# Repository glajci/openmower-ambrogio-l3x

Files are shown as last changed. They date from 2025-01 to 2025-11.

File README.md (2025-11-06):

# Openmower - Ambrogio - L3x
Convert Ambrogio L30 mower to [OpenMower](https://openmower.de) powered mower.

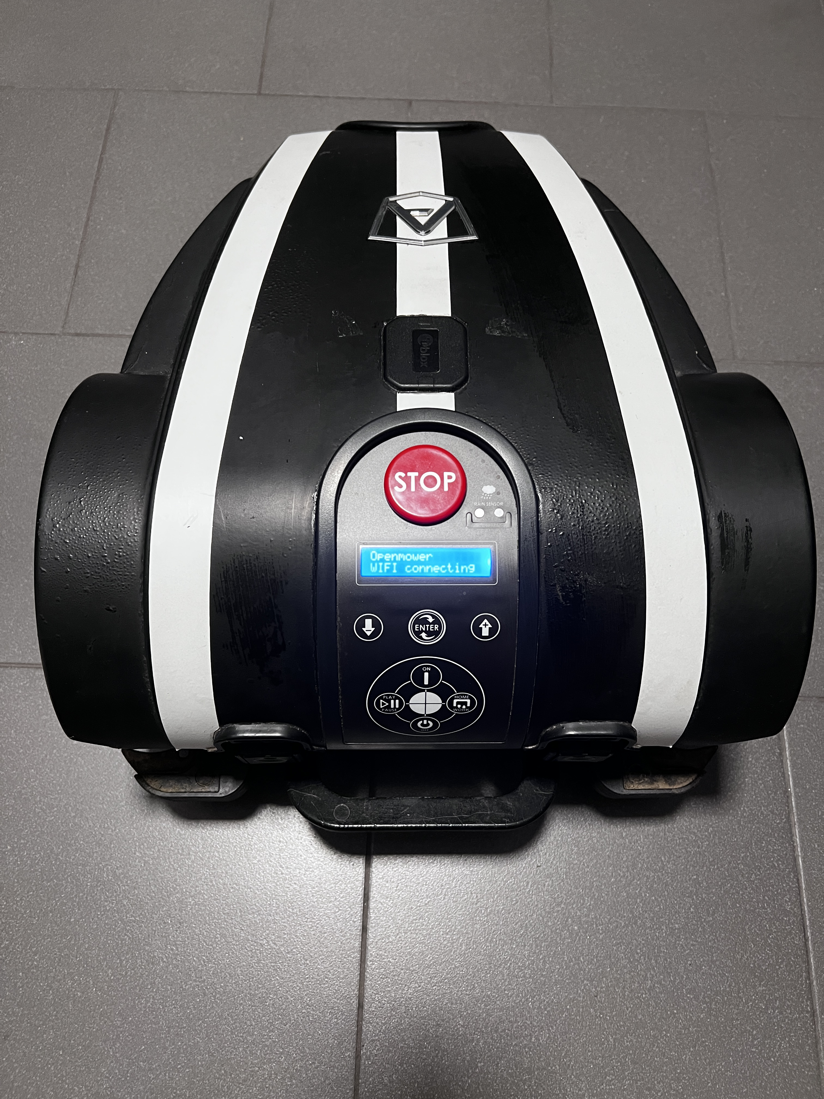
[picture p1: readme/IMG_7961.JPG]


> [!WARNING]
> Please be aware that this is a working prototype, any modifications to the mower are made at your own risk.

> [!NOTE]
> Ambrogio L30 mower was used in this project, but it should work with Viper C6, Stiga Autoclip 225 and similar as well.

# Features

* All of the features of the [OpenMower](https://openmower.de)
* Rain sensor
* Lift Sensor
* Emergency Stop push button
* Cutting with 25cm
* Integrated built-in display and top cover buttons (optional)

> Comparison with Yard Force Classic 500
> * Pros:
>   * Increased cutting width (25cm)
>   * More powerful, no issues with cutting the grass
>   * Turns easier due to its geometry
>   * No issues with steep climbs (no wheel spikes needed)
>
> * Cons:
>   * Louder mowing motor (while using 4 points steel cutting blade, perhaps 12 points plastic disc is quieter?)
>   * Tilt sensor not connected

# Hardware and Tools

You will need:

* Ambrogio L30 mower or similar (Viper C6, Stiga Autoclip 225 ...)
* [Open Mower Hardware Kit](https://shop.devops.care/10-openmower)
* [Ardusimple simpleRTK2B – Basic Starter Kit](https://www.ardusimple.com/product/simplertk2b-basic-starter-kit-ip65/)
* Raspberry Pi 4 (minimum 2GB)
* SD Card 16GB+
* USB Wi-Fi Dongle
* Yard Force Classic 500 wiring harnesses (can be created from the scratch as well)
* 3D printer
* [Vesc Tool Free](https://vesc-project.com/node/17)
* 16x2 LCD Display with I2C adapter (optional)
* 2 relay module (optional)

# Assembly

## Docking station

Remove all the original electronics from the docking station.

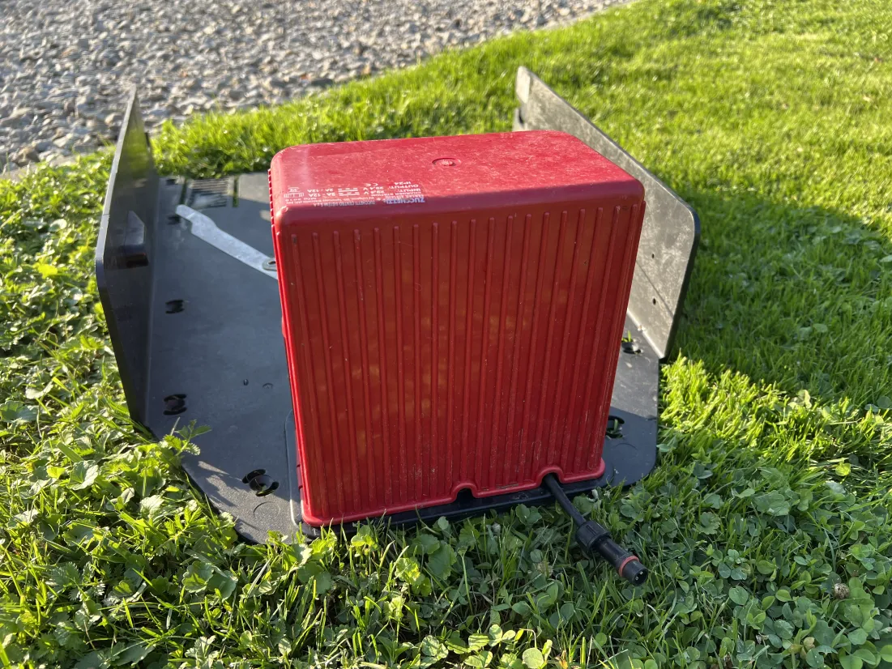
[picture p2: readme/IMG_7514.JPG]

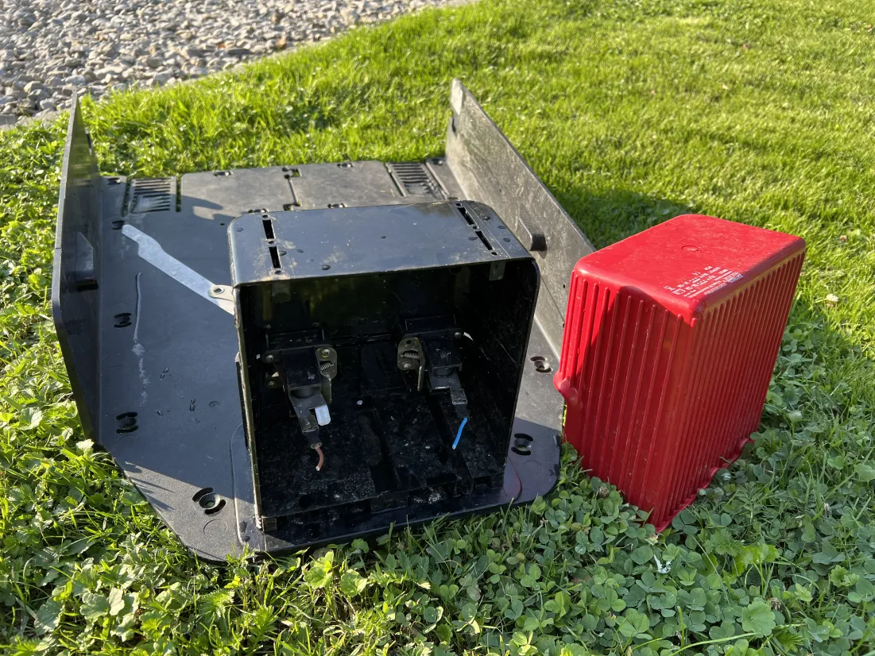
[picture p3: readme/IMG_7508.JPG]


Place 2 expansions plugs in 2 holes.

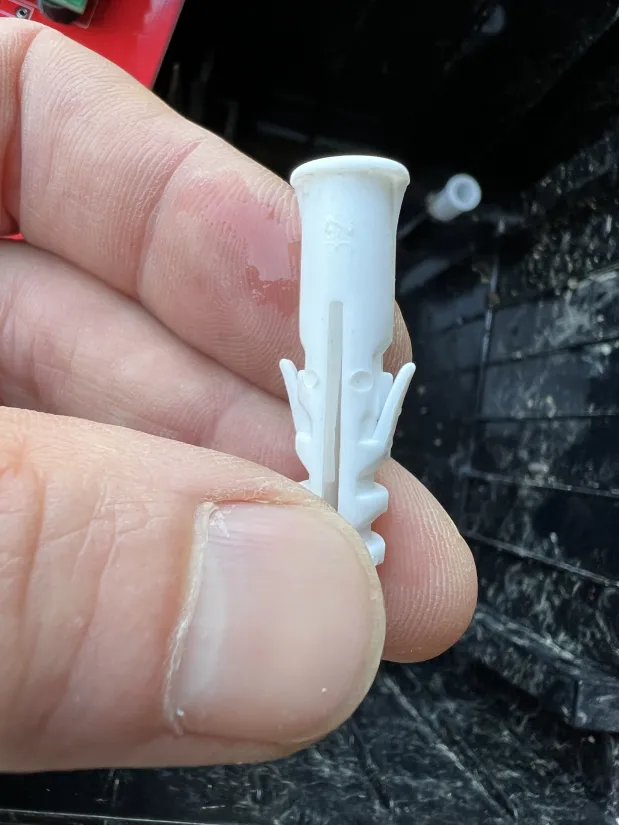
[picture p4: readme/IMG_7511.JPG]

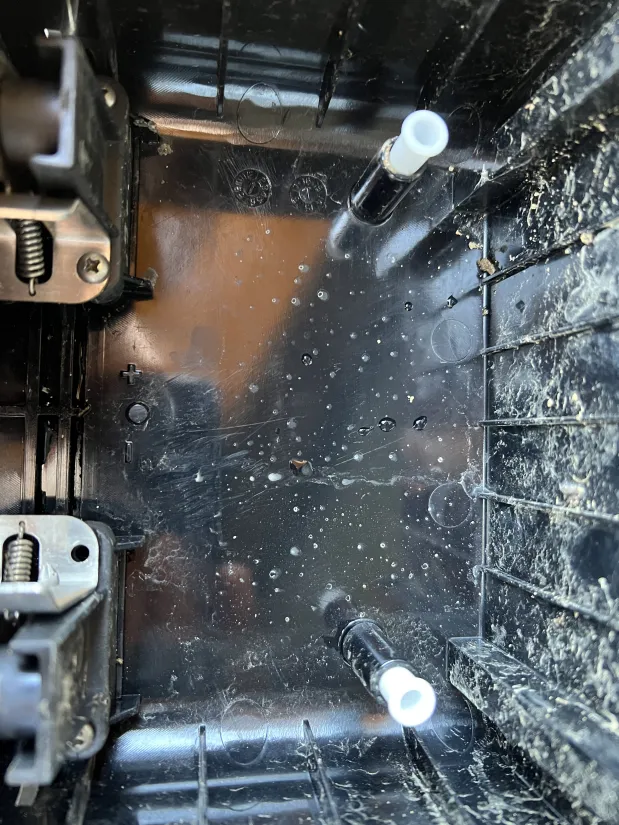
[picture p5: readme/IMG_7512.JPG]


Screw the DC/DC board

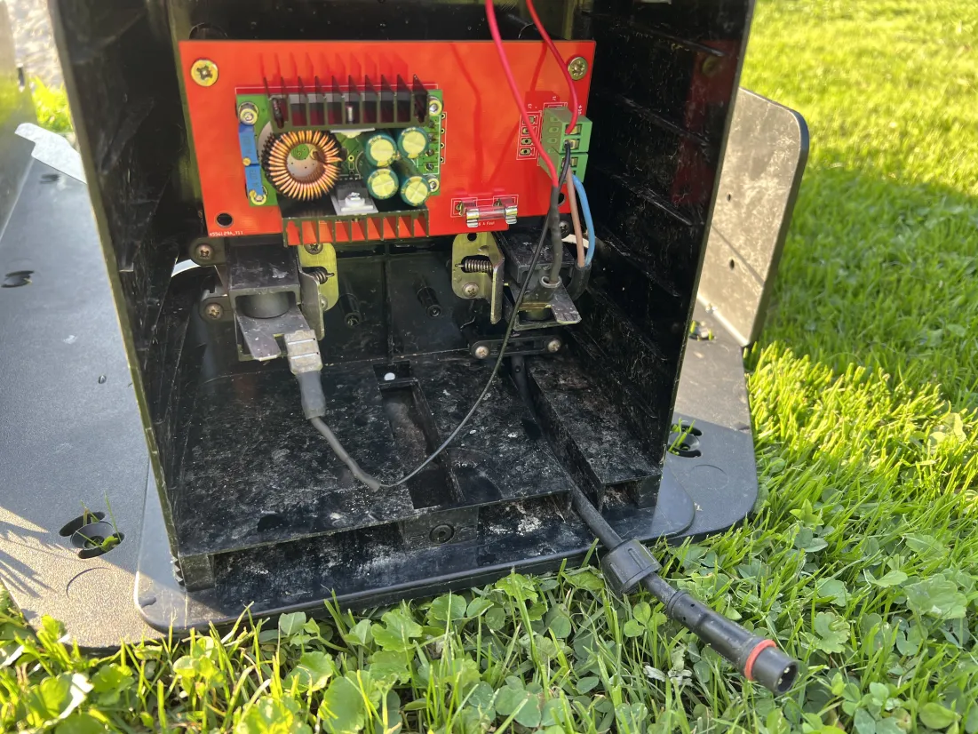
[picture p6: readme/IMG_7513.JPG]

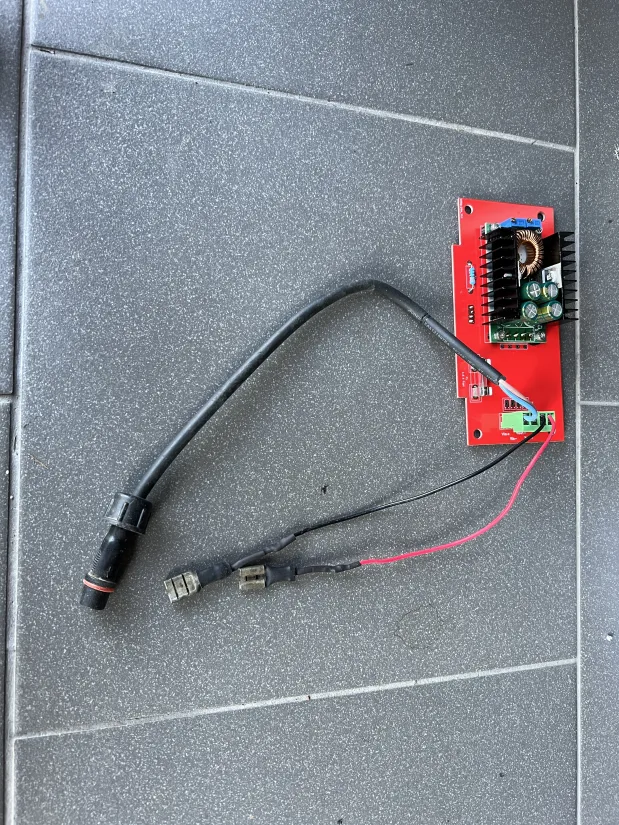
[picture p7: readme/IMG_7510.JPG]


> [!NOTE]
> Plug from the YardForce Classic 500 power supply was used here but the original Ambrogio power supply will work as well.
(find the positive and negative wires and connect it appropriately to the DC/DC board)

> [!NOTE]
> For all the voltage and current adjustments please follow the official [OpenMower](https://openmower.de) documentation.

## The mower

Remove all the original mower electronics.
Cut the plastic elements (see the pictures below) to make the place for the mainboard.

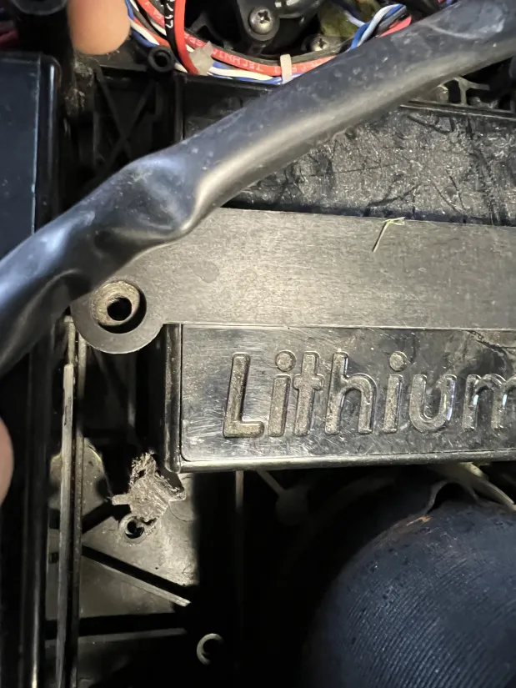
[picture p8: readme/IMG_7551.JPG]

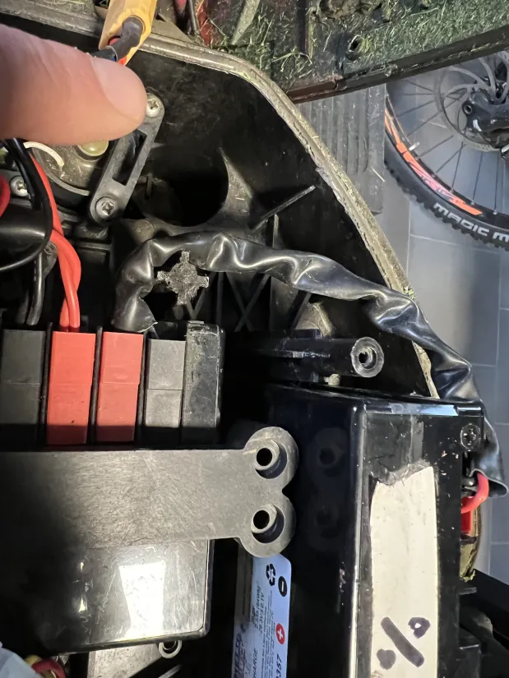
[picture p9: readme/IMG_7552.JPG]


### Prepare the motor Hall sensor wires.

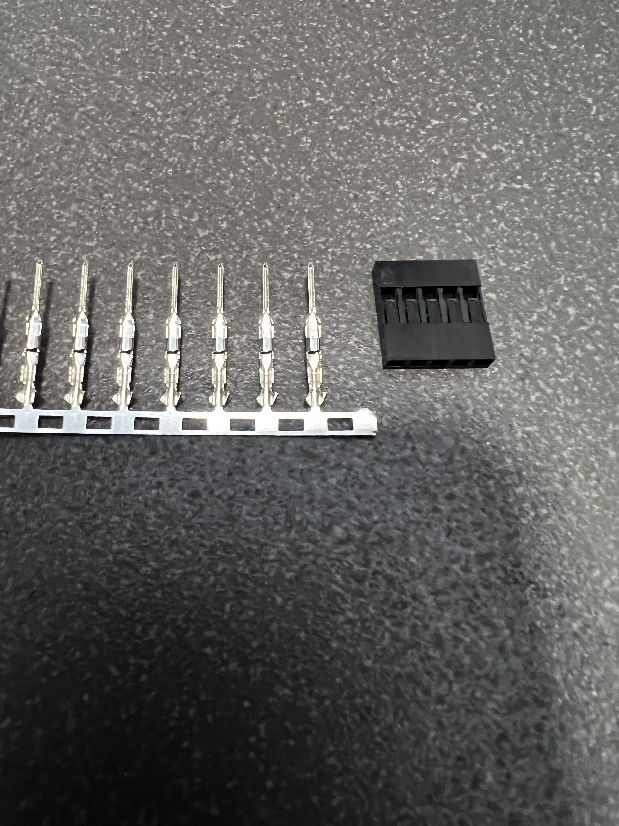
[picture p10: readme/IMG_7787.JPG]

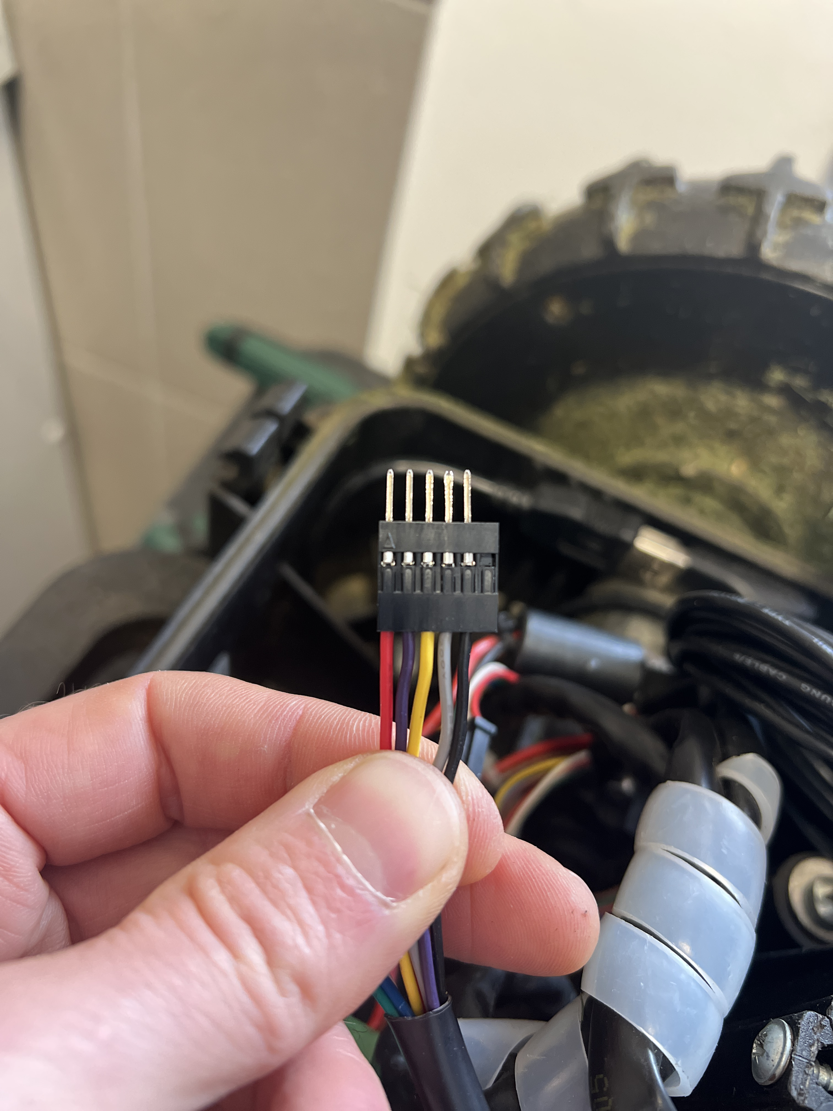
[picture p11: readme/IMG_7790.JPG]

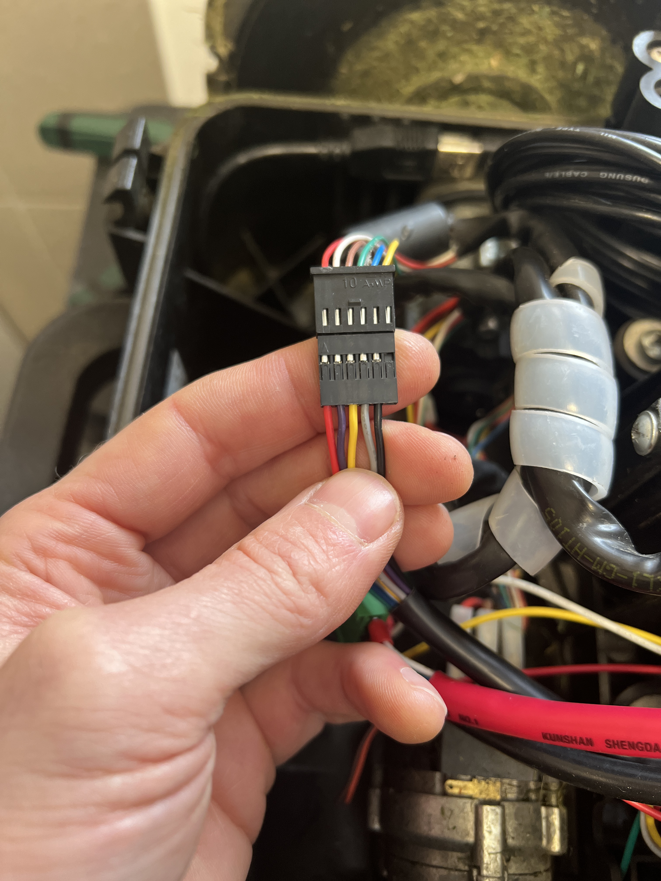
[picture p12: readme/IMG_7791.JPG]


### Prepare the motor power wires.

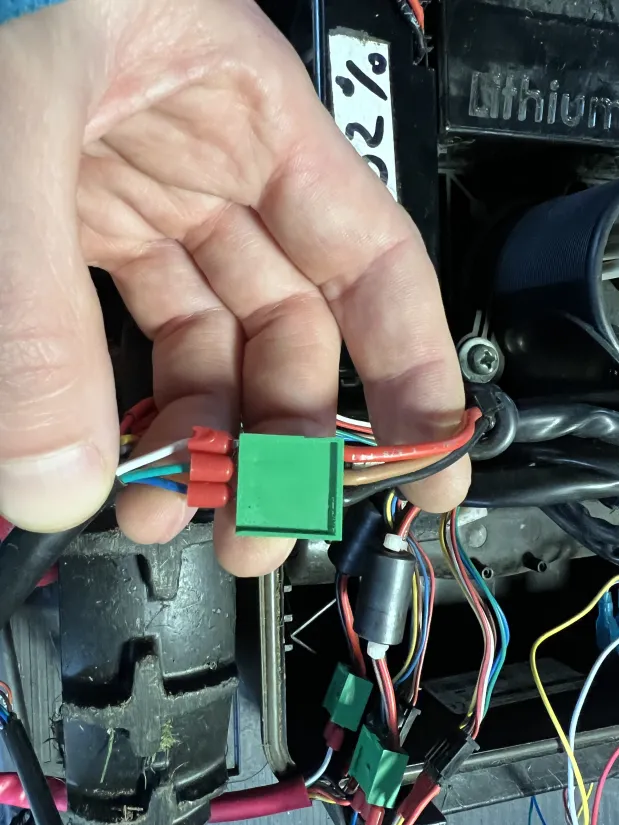
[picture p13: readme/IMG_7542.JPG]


### Ambrogio L30 Opemnower wiring diagram.

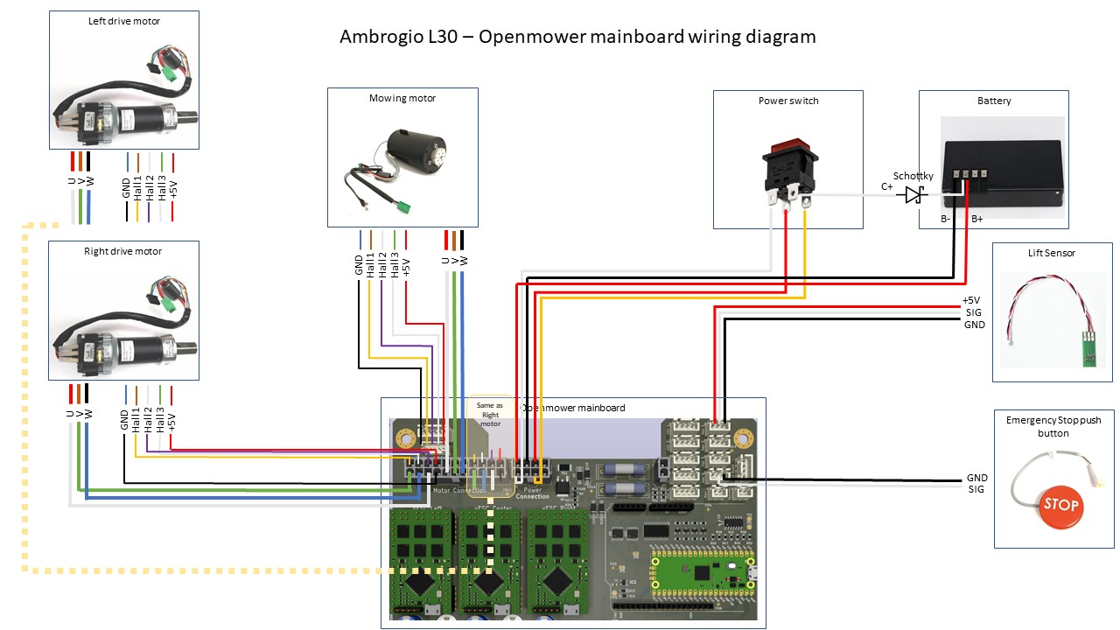
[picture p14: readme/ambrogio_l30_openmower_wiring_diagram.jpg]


> [!NOTE]
> YardForce Classic 500 wiring harness was used, since it fits to the OpenMower mainboard sockets, but it can be created from the scratch as well.

> [!NOTE]
> Crimped terminals for the motor power wires were used.

> [!NOTE]
> All 3 motor harnesses have the same colouring.

### Install the main switch into the mower body (power switch from the YardeForce Classic 500 was used here)
> [!NOTE]
> No need to install the power button if 2 relay module and top cover power buttons are integrated (see later in this tutorial).

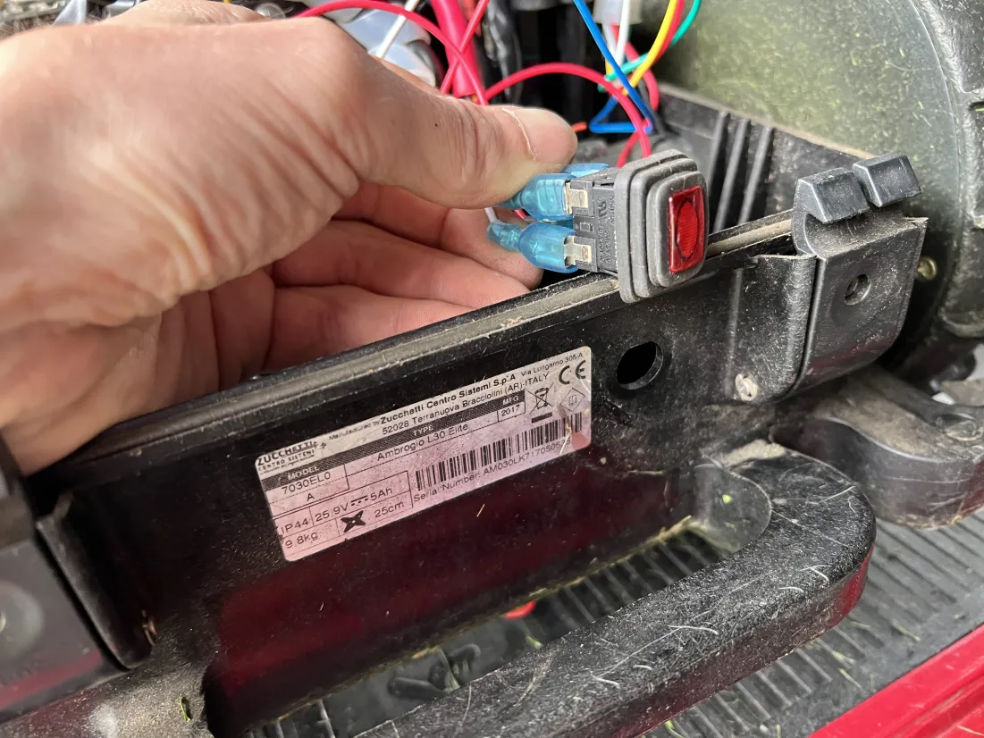
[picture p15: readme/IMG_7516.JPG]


Remove Ambrogio's power supply socket

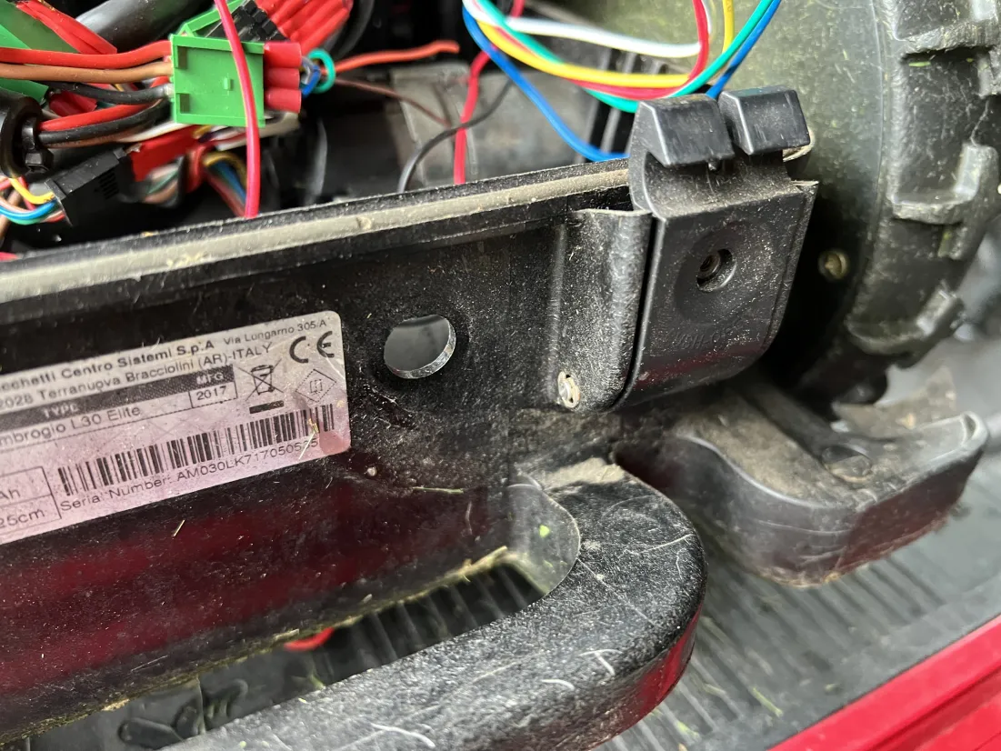
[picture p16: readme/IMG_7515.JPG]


Extend the circular hole to give it a rectangular shape with proper dimensions

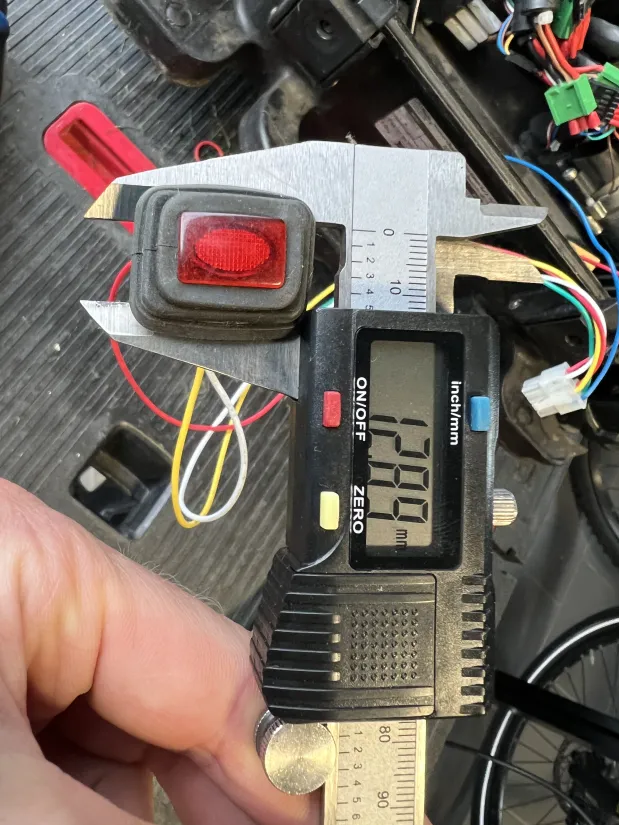
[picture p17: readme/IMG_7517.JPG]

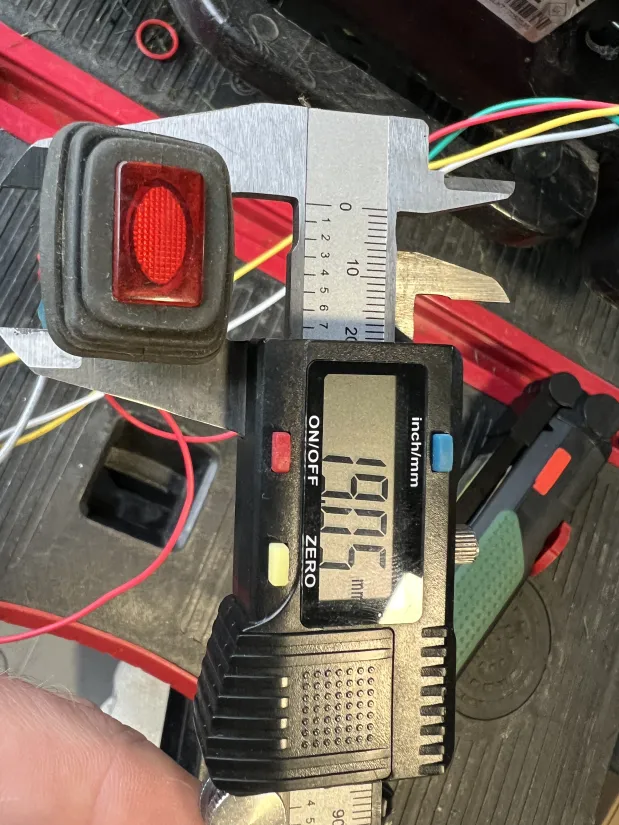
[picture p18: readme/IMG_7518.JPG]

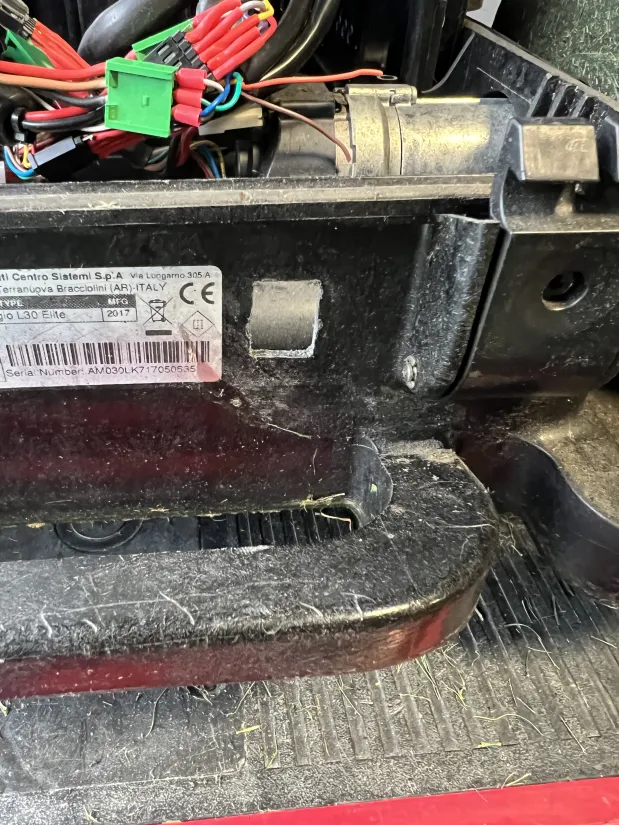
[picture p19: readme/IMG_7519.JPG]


Insert the power switch

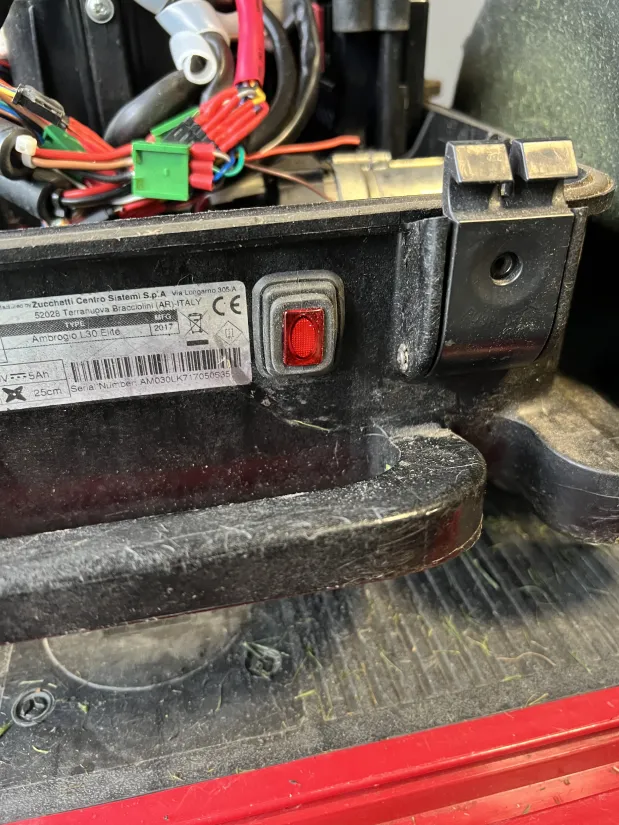
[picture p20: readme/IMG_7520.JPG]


### Prepare the power supply harness.
> [!NOTE]
> Since the Ambrogio batteries have just 2 wires (positive and negative), Shottky diode was used to create separate charge + and battery + signals. (Original YardForce Classic 500 battery plug was use here)

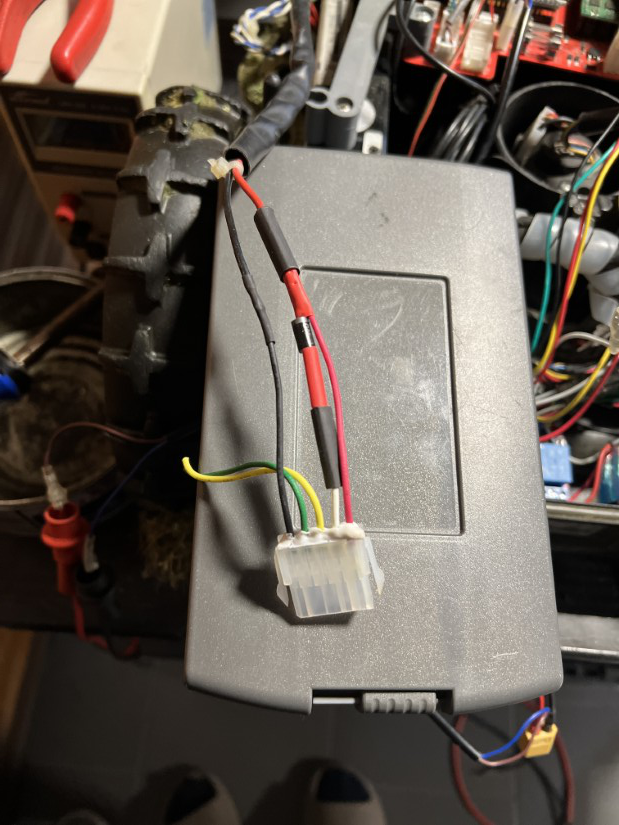
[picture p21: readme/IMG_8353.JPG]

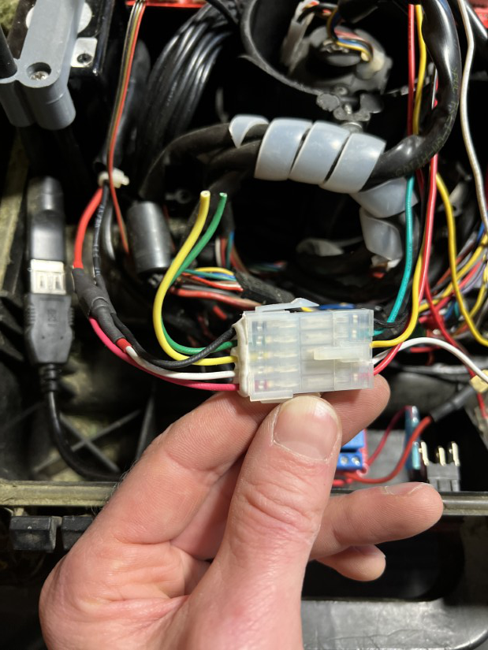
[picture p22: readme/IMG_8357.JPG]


Prepare the power connectors

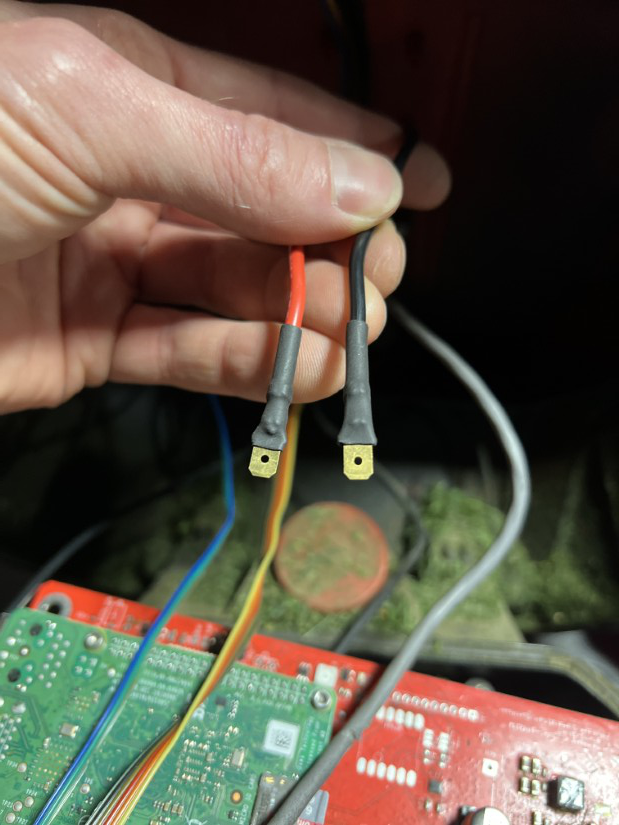
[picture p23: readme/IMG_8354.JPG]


Connect it to the OpenMower mainboard.

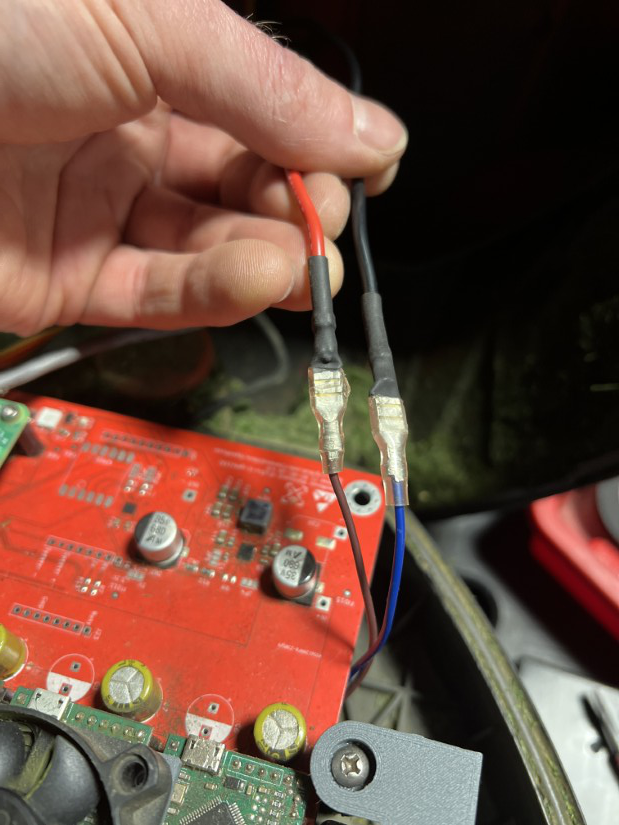
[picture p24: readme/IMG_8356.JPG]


Connect OpenMower with power button (2 relay module visible on the pictures is optional - see later in this tutorial).

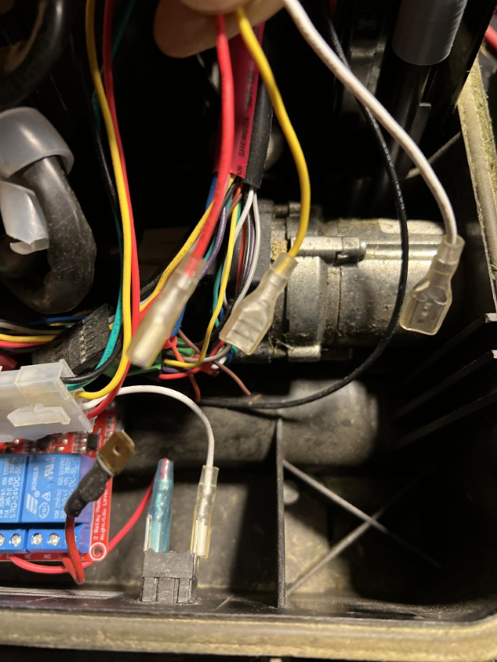
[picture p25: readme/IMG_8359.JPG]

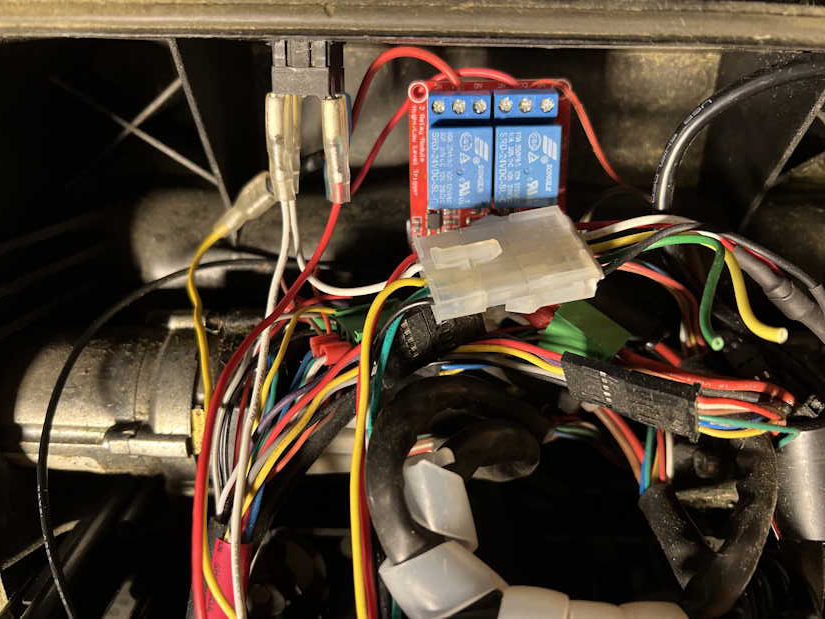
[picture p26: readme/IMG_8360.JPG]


### Prepare the lift sensor cable.

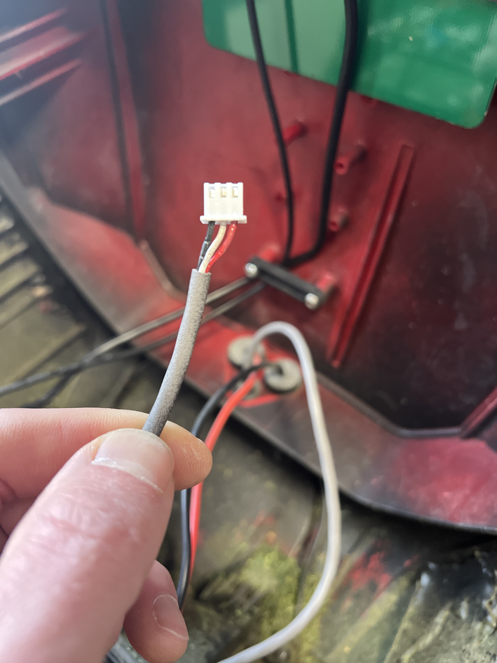
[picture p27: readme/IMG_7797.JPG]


### Install the mainboard

Unscrew the original left and right battery holders.
Print and screw the mainboard holders.
> [!NOTE]
> You will find all the 3d models in this repository.

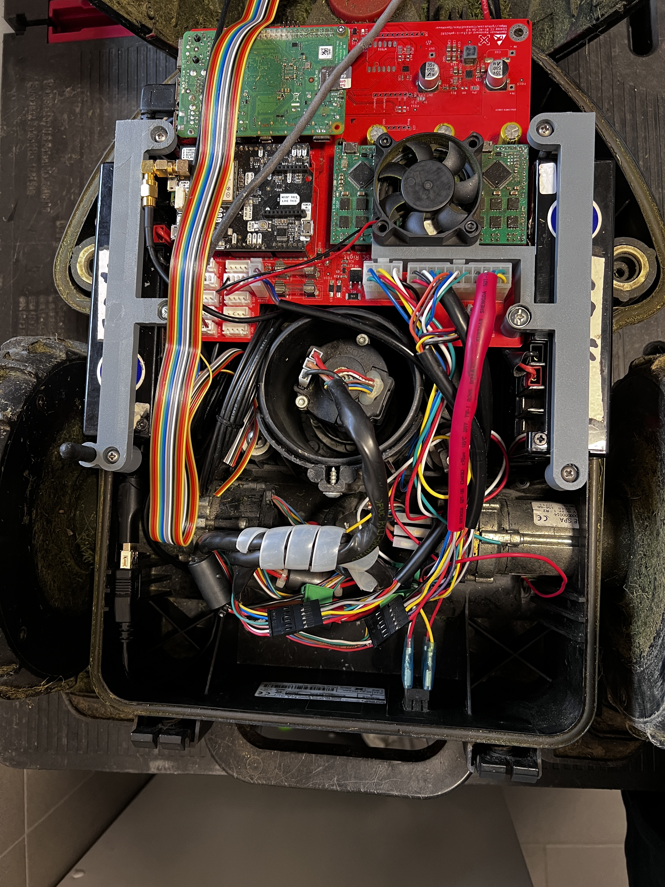
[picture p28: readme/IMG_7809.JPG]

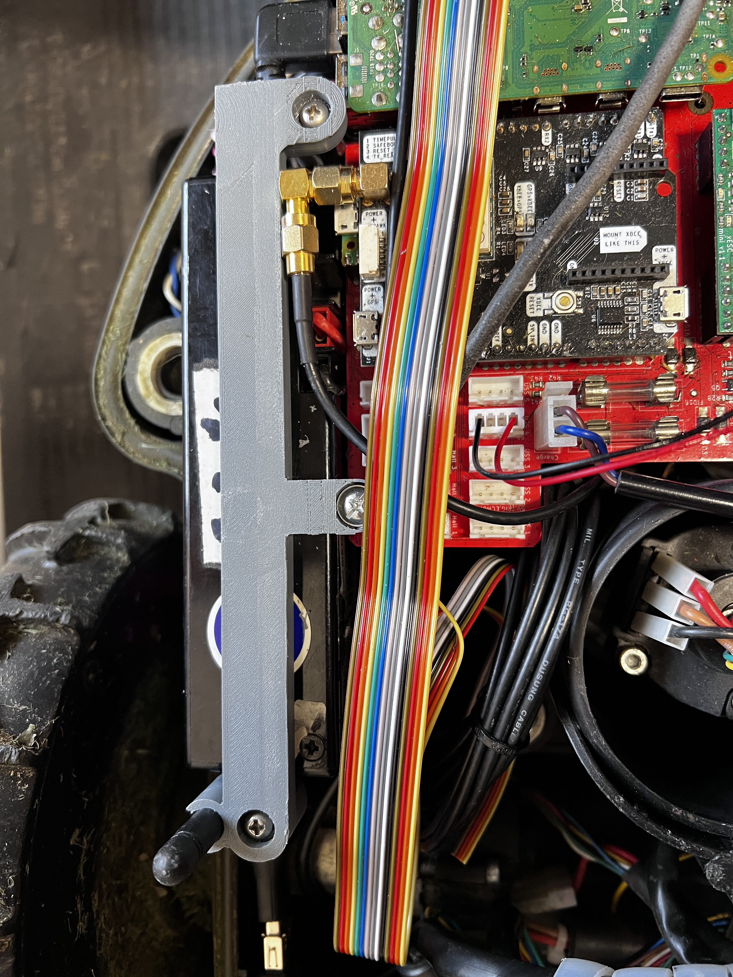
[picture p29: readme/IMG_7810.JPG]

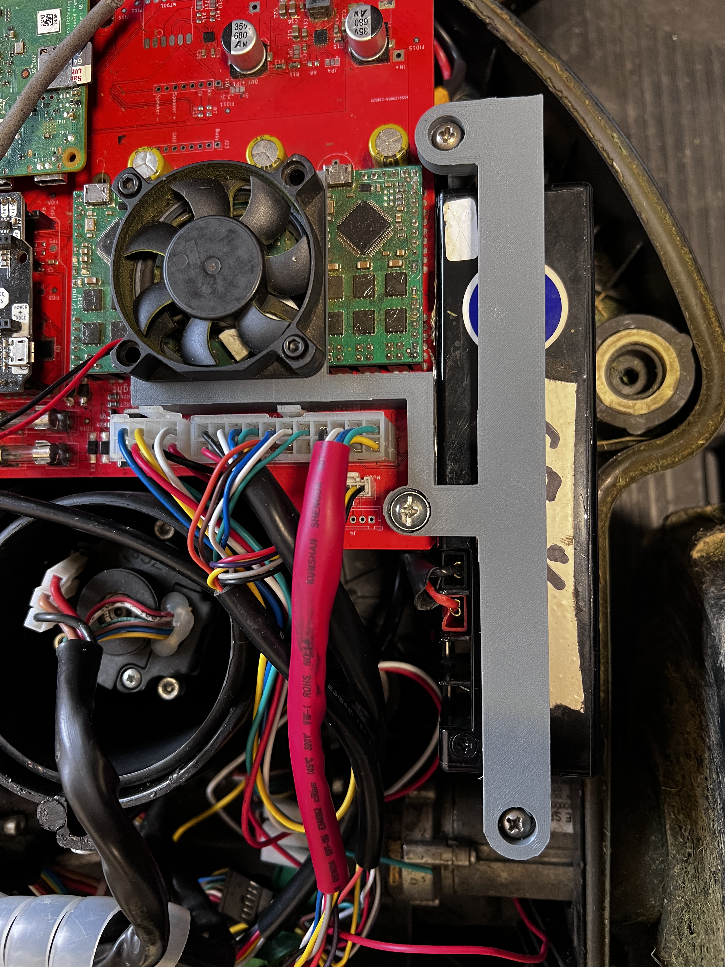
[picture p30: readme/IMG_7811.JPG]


### Prepare the top cover panel harness.

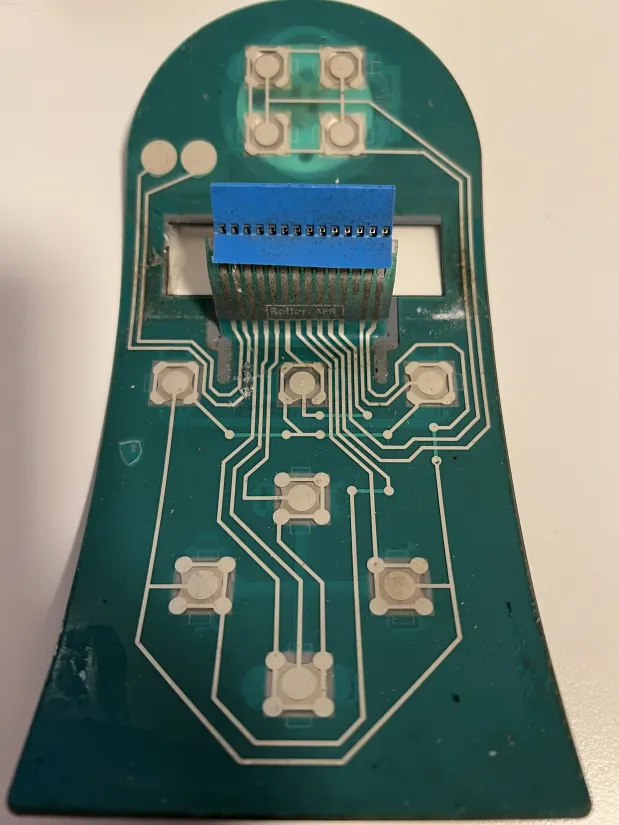
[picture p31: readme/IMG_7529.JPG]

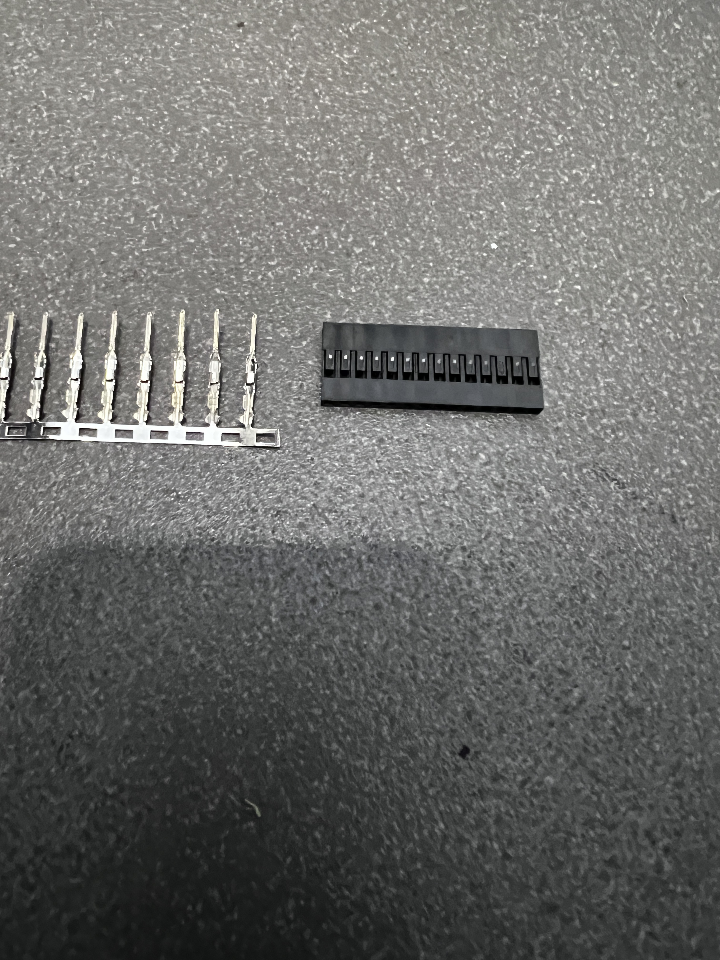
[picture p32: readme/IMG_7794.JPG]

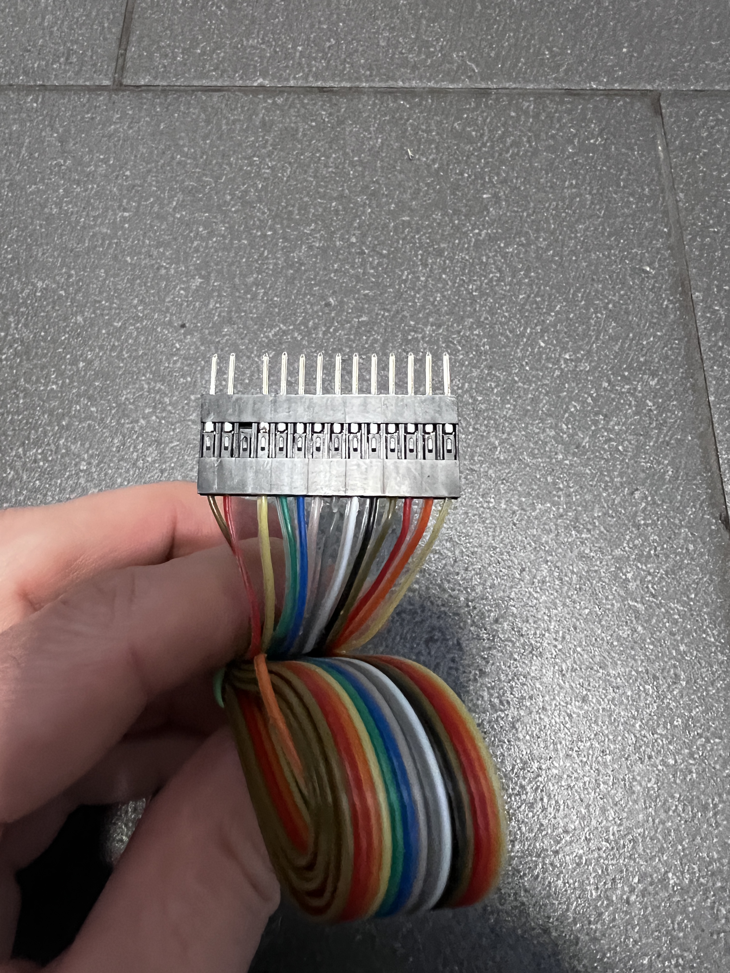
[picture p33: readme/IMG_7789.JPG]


### Connect Emergency Stop push button and rain sensor to the mainboard.

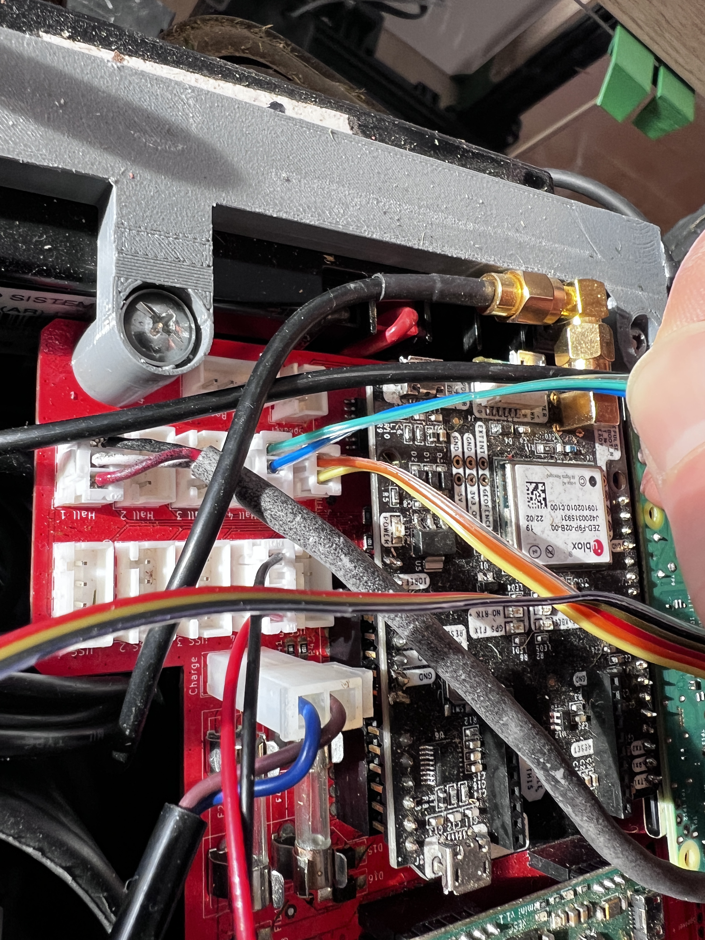
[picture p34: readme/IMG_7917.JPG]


### (Optional) Install the GPS antenna in the mower's body

> [!NOTE]
> There is no need to cut the hole in the mower's body for the GPS antena. It can work inside of the mower as well.
> Installing it like in the pictures below, improve the signal quality

Cut the hole in the mower body.

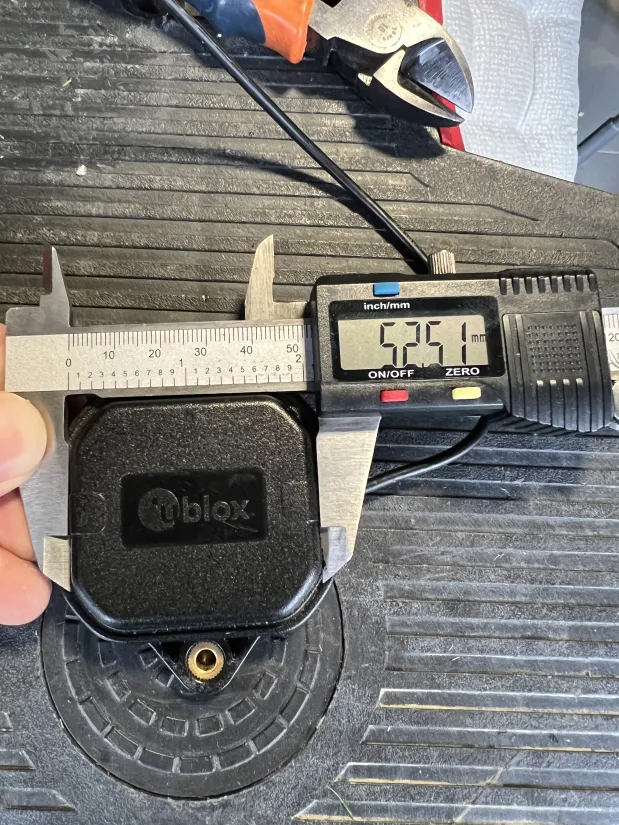
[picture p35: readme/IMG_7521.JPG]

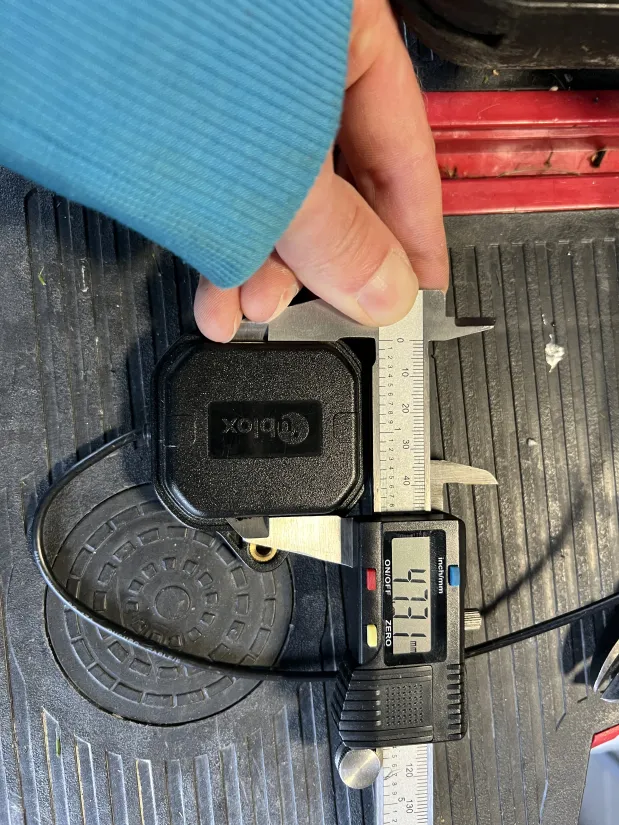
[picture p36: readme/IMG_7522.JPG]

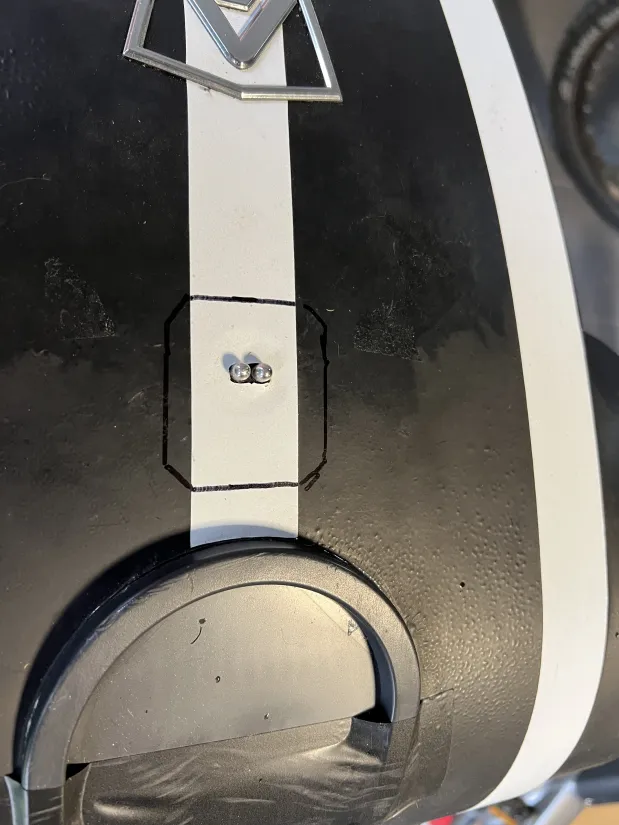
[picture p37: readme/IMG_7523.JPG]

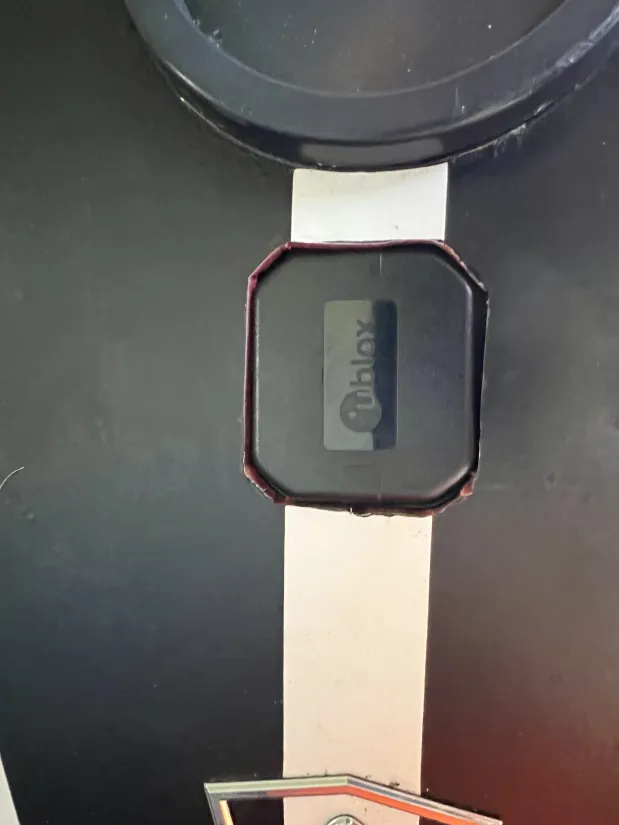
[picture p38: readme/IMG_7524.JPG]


Install the GPS antena in the body and seal it with the silicone.

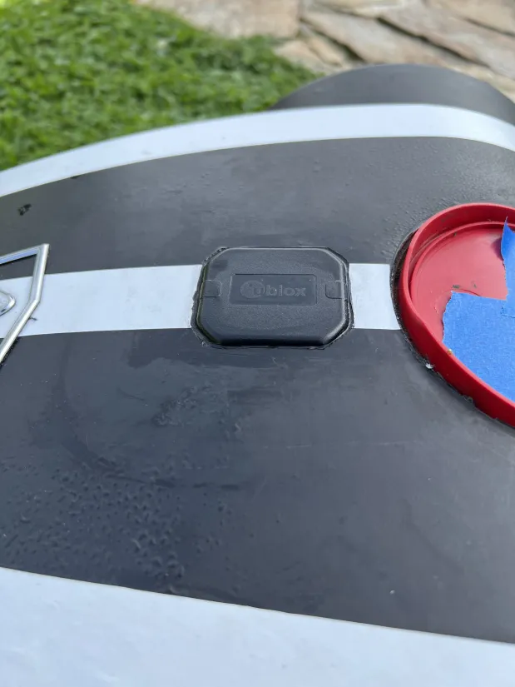
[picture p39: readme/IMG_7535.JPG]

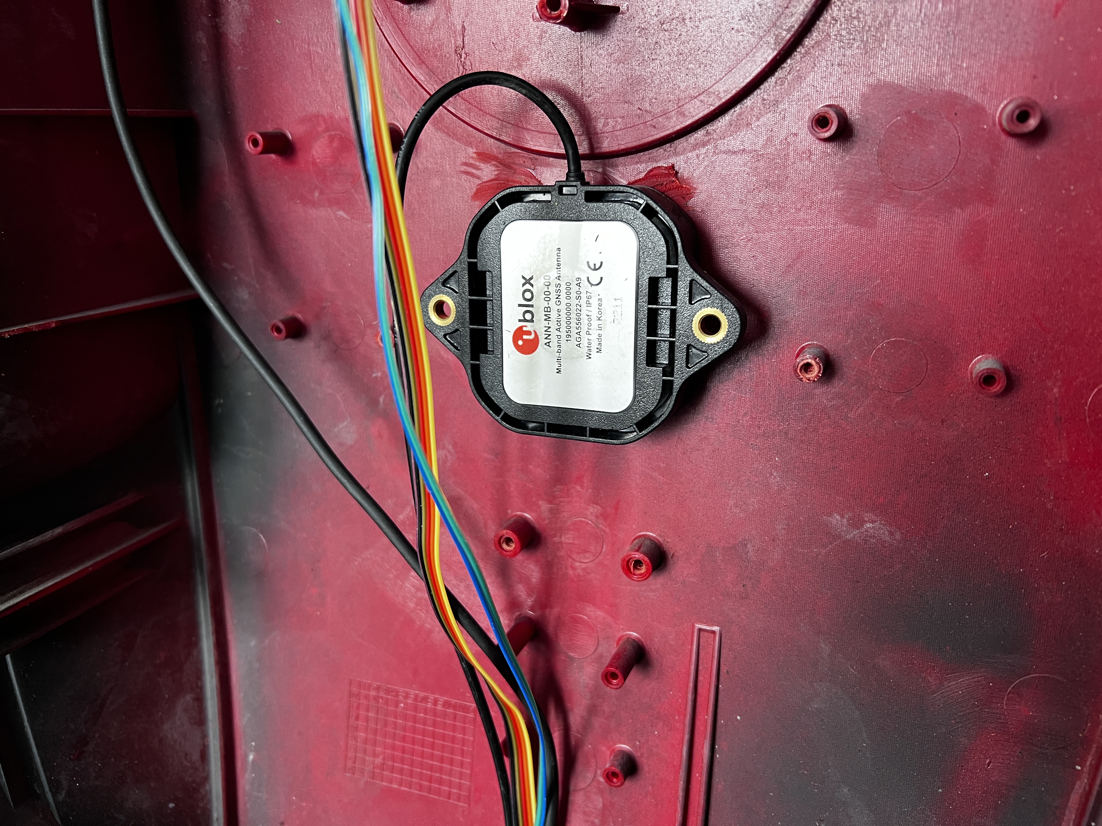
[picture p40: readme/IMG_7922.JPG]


Install a piece of steel material from the bottom as the antenna shield.



### (Optional) Install the 2 relay module as power switch.

Use exaclty the same 2 relay module as on the picture below.



Solder the wires from the bottom.



Prepare the wires and the plug for on/off buttons.



Print and screw the 2 relay module adapter.




Connect as show below.





### (Optional) Install the display.

Print the 3d model.



Place LCD display in the holder.




Install the display in the mower.



Use 40 pin female-female IDC Cable and Raspberry Pi expansion board to create the wiring harness for the display and for the top cover panel as shown below.








Plug expansion board in the Openmower mainboard.
Plug Raspberry Pi in the expansion board as shown below.




Connect the other end of the 40 pin cable with the display and with the top cover panel as shown below. 






## Software

### Install the OpenMower on the Raspberry Pi

Please follow the official [OpenMower](https://openmower.de) documentation for more details.

### Upload configuration files to xESC

Connect to the xESC which is going to be the mowing motor controller using USB to microUSB cable.

Open Vesc Tool [Vesc Tool Free](https://vesc-project.com/node/17).

Load the following configuration file and write it to the mowing motor xESC.

[Ambrogio_L30_Mower_Motor_10A.xml](configuration/Ambrogio_L30_Mower_Motor_10A.xml)

Connect to the xESC's which are going to be the drive motors controllers using USB to microUSB cable.

Open Vesc Tool [Vesc Tool Free](https://vesc-project.com/node/17).

Load the following configuration file and write it to the drive motor xESC.

[Ambrogio_L30_Drive_Motor.xml](configuration/Ambrogio_L30_Drive_Motor.xml)

> [!NOTE]
> The xESC configuration files provided above are suited for Ambrogio L30 motor. Play with Vesc Tool to find best settings for another motors.

> [!NOTE]
> Please follow the official [Vesc](https://vesc-project.com/documentation) documentation for more details.

### Modify the mower_config.txt

> [!NOTE]
> Please follow the official [OpenMower](https://openmower.de) documentation for more details.

Define the wheel distance and wheel ticks

Set distance between wheels in m
```
export OM_WHEEL_DISTANCE_M=${WHEEL_DISTANCE_M:-0.355}
```
Set default ticks/m
```
export OM_WHEEL_TICKS_PER_M=${OM_WHEEL_TICKS_PER_M:-1830.0}
```
Define the GPS antena offsets, according to the antena position (depends on where the GPS antena is located in the mower)

Set default GPS antenna offset (Example)
```
export OM_ANTENNA_OFFSET_X=${OM_ANTENNA_OFFSET_X:-0.08}
export OM_ANTENNA_OFFSET_Y=${OM_ANTENNA_OFFSET_Y:-0.0}
```

Set the following configuration of the emergency inputs
```
export OM_EMERGENCY_INPUT_CONFIG="L, I, I, !S"
export OM_EMERGENCY_LIFT_PERIOD="100"
export OM_EMERGENCY_TILT_PERIOD="2500"
```

### The display

Display connects to the OpenMower's MQTT, to both, read and send MQTT messages.

#### Features

* Show actual OpenMower state, sensors values (GPS accuracy, Battery voltage, Charging)
* Start, Pause, Dock, Reset Emergency, Skip area, Skip path actions
* Sleep timer turns off display after 60s, wakes on any button press

#### Tools

You will need:

* A 16x2 lcd i2c display.
* A Raspberry Pi expansion board.
* A 40 pin cable.
* A source code files (included in this repository)
* A computer (presumably, the one you are reading this on!)

##### Setup

Edit [config.py](pi_zero_w/display/src/config.py) file and set the IP of the Openmower's Rpi Ehternet device.
```
mqtt_host = "172.16.78.1"
mqtt_port = 1883
```

> [!NOTE]
> To determine the IP of the Openmower's Rpi Ehternet device, SSH to Openmower Rpi and execute the following:
```
putty -ssh openmower.local:22 -l openmower -pw openmower 
hostname -I
```

SSH to Openmower Rpi and create /home/openmower/display directory
```
putty -ssh openmower.local:22 -l openmower -pw openmower
sudo mkdir display
```

Copy all python (*.py) files from [display folder](display) to Rpi.
```
pscp -r -pw openmower {your_location}\display\*.* openmower@openmower.local:/home/openmower/display
```

SSH to Openmower Rpi and enable I2C
```
putty -ssh openmower.local:22 -l openmower -pw openmower
sudo raspi-config
```

Then navigate: Interface Options  →  I2C  →  Yes  →  Finish

Then reboot:
```
sudo reboot
```

SSH to Openmower Rpi and install paho-mqtt
```
putty -ssh openmower.local:22 -l openmower -pw openmower
sudo apt update
sudo apt install python3-paho-mqtt -y
```

Make main.py file executable
```
chmod +x /home/openmower/display/main.py
```

Create new systemd service file
```
sudo nano /etc/systemd/system/omdisplay.service
```

Paste the following content
```
[Unit]
Description=My Python Startup Script
After=network.target

[Service]
ExecStart=/usr/bin/python3 /home/openmower/display/main.py
WorkingDirectory=/home/openmower/display
StandardOutput=inherit
StandardError=inherit
Restart=always
User=openmower

[Install]
WantedBy=multi-user.target
```

Enable and start the service
```
sudo systemctl daemon-reload
sudo systemctl enable omdisplay.service
sudo systemctl start omdisplay.service
```

Omdisplay.service will from now on auto-start whenever you supply power to Rpi.

To check status
```
systemctl status omdisplay.service
```

To see the logs
```
journalctl -u omdisplay.service -f
```

After successful installation you should see something like that:

Main screen

Turn on the OpenMower, it will try to establish MQTT connection.

Demo picture

When the connection is established you should be able to operate the OpenMower:

Demo picture

Pressing the Up, Down or Enter button on the top cover panel, you will enter the menu.
Depending on the current mower status you will see one of the submenus.





Using Up and Down arrows on the top cover panel, you can scroll the available submenus.
Pressing Enter will execute the selected menu action (example: Reset Emergency) and return to main view.

When OpenMower operates you will see one of the following statuses.




# Summary

Hopefully, you will manage to follow the instructions and by the end of the day you will enjoy the perfect lawn.






In case of any support request visit the excellent OpenMower community on the dedicated [Discord](https://discord.gg/jE7QNaSxW7) channel.

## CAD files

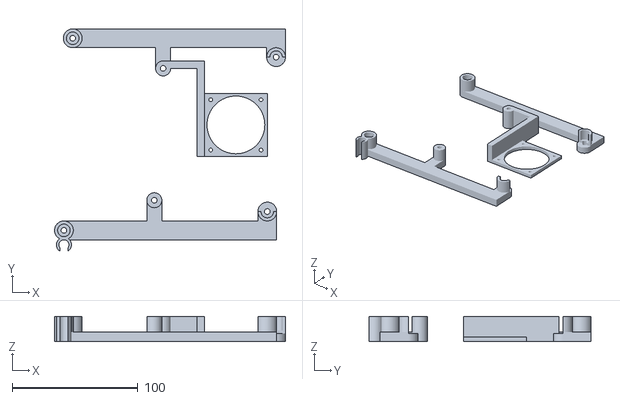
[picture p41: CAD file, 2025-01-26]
print/Ambrogio L30 Battery Mainboard holder.stl
184.0 x 177.0 x 20.0

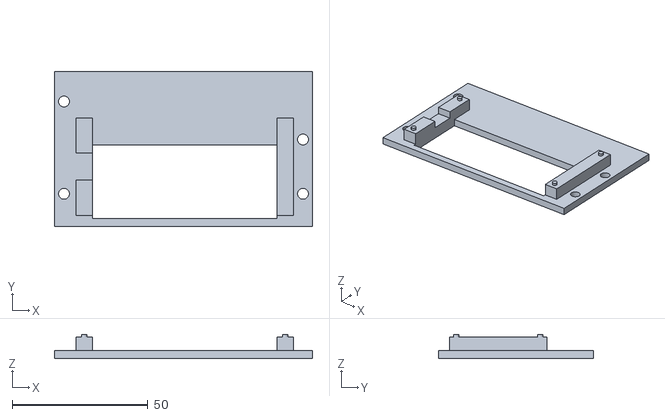
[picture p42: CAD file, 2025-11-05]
print/Ambrogio L30 display holder.stl
95.0 x 57.0 x 9.00

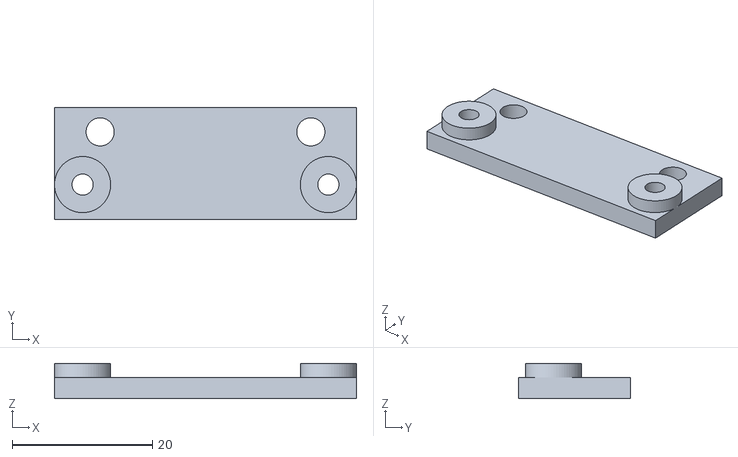
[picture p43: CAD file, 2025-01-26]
print/Ambrogio L30 Power switch board holder.stl
43.0 x 16.0 x 5.00

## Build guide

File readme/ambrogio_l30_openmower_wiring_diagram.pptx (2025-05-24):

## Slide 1

Left drive motor

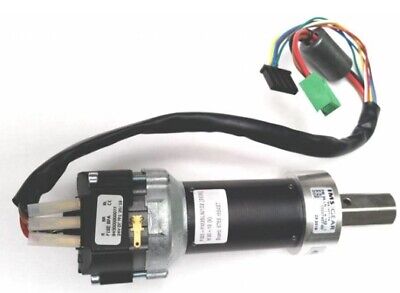
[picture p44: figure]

Ambrogio L30 – Openmower mainboard wiring diagram

Mowing motor

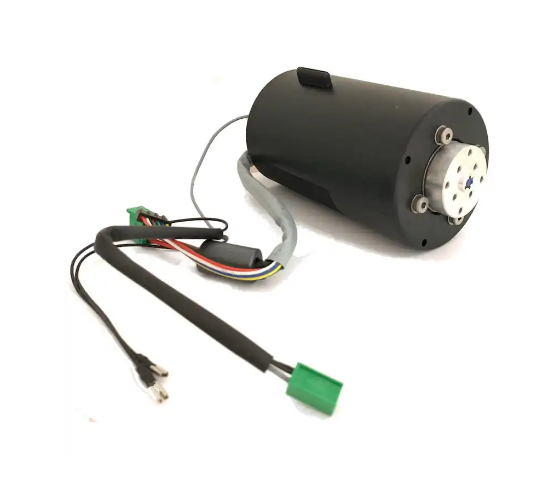
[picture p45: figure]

Power switch

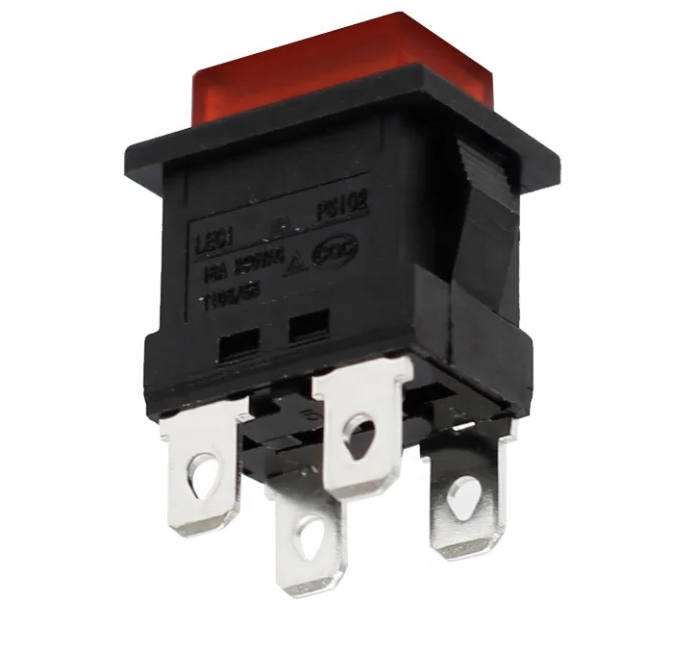
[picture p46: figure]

Battery

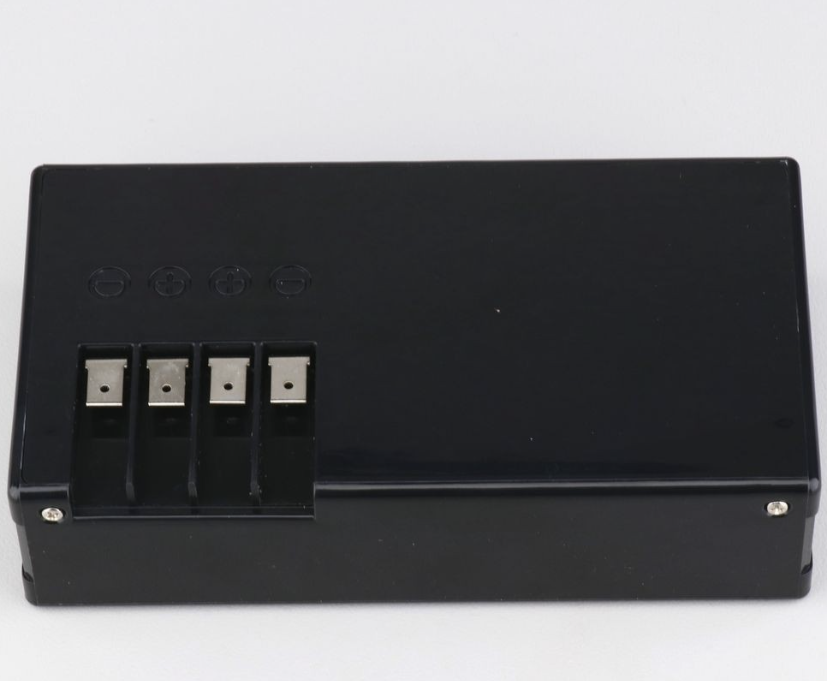
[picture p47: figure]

Hall1

GND

Hall2

Hall3

+5V

W

V

U

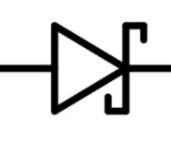
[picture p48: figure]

C+

Schottky

B-

B+

Right drive motor

Hall1

GND

Hall2

Hall3

+5V

W

V

U

Lift Sensor

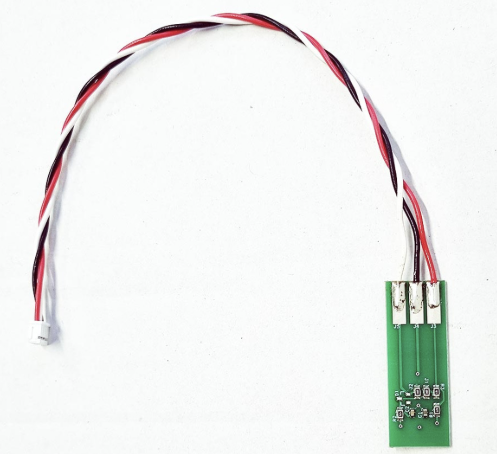
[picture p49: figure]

+5V

SIG

GND

W

V

U

Hall1

GND

Hall2

Hall3

+5V

Openmower mainboard

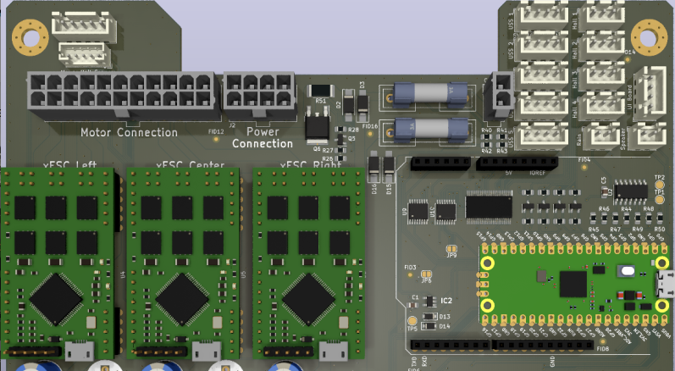
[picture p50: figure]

Same as Right motor

Emergency Stop push button

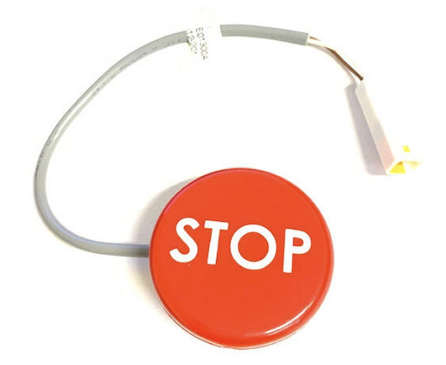
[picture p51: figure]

GND

SIG

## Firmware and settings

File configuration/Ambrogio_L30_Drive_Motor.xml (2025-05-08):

<?xml version="1.0" encoding="UTF-8"?>
<MCConfiguration>
    <pwm_mode>1</pwm_mode>
    <comm_mode>0</comm_mode>
    <motor_type>2</motor_type>
    <sensor_mode>0</sensor_mode>
    <l_current_max>3</l_current_max>
    <l_current_min>-3</l_current_min>
    <l_in_current_max>6</l_in_current_max>
    <l_in_current_min>-6</l_in_current_min>
    <l_abs_current_max>15</l_abs_current_max>
    <l_min_erpm>-100000</l_min_erpm>
    <l_max_erpm>100000</l_max_erpm>
    <l_erpm_start>0.8</l_erpm_start>
    <l_max_erpm_fbrake>300</l_max_erpm_fbrake>
    <l_max_erpm_fbrake_cc>1500</l_max_erpm_fbrake_cc>
    <l_min_vin>8</l_min_vin>
    <l_max_vin>40</l_max_vin>
    <l_battery_cut_start>6</l_battery_cut_start>
    <l_battery_cut_end>6</l_battery_cut_end>
    <l_slow_abs_current>0</l_slow_abs_current>
    <l_temp_fet_start>85</l_temp_fet_start>
    <l_temp_fet_end>90</l_temp_fet_end>
    <l_temp_motor_start>85</l_temp_motor_start>
    <l_temp_motor_end>100</l_temp_motor_end>
    <l_temp_accel_dec>0.15</l_temp_accel_dec>
    <l_min_duty>0.005</l_min_duty>
    <l_max_duty>0.95</l_max_duty>
    <l_watt_max>1.5e+06</l_watt_max>
    <l_watt_min>-1.5e+06</l_watt_min>
    <l_current_max_scale>1</l_current_max_scale>
    <l_current_min_scale>1</l_current_min_scale>
    <l_duty_start>1</l_duty_start>
    <sl_min_erpm>150</sl_min_erpm>
    <sl_min_erpm_cycle_int_limit>1100</sl_min_erpm_cycle_int_limit>
    <sl_max_fullbreak_current_dir_change>10</sl_max_fullbreak_current_dir_change>
    <sl_cycle_int_limit>62</sl_cycle_int_limit>
    <sl_phase_advance_at_br>0.8</sl_phase_advance_at_br>
    <sl_cycle_int_rpm_br>80000</sl_cycle_int_rpm_br>
    <sl_bemf_coupling_k>600</sl_bemf_coupling_k>
    <hall_table__0>-1</hall_table__0>
    <hall_table__1>1</hall_table__1>
    <hall_table__2>3</hall_table__2>
    <hall_table__3>2</hall_table__3>
    <hall_table__4>5</hall_table__4>
    <hall_table__5>6</hall_table__5>
    <hall_table__6>4</hall_table__6>
    <hall_table__7>-1</hall_table__7>
    <hall_sl_erpm>2000</hall_sl_erpm>
    <foc_current_kp>1.2072</foc_current_kp>
    <foc_current_ki>1758.55</foc_current_ki>
    <foc_f_zv>25000</foc_f_zv>
    <foc_dt_us>0.12</foc_dt_us>
    <foc_encoder_inverted>0</foc_encoder_inverted>
    <foc_encoder_offset>180</foc_encoder_offset>
    <foc_encoder_ratio>7</foc_encoder_ratio>
    <foc_encoder_sin_gain>1</foc_encoder_sin_gain>
    <foc_encoder_cos_gain>1</foc_encoder_cos_gain>
    <foc_encoder_sin_offset>1.65</foc_encoder_sin_offset>
    <foc_encoder_cos_offset>1.65</foc_encoder_cos_offset>
    <foc_encoder_sincos_filter_constant>0.5</foc_encoder_sincos_filter_constant>
    <foc_sensor_mode>2</foc_sensor_mode>
    <foc_pll_kp>2000</foc_pll_kp>
    <foc_pll_ki>30000</foc_pll_ki>
    <foc_motor_l>0.0012072</foc_motor_l>
    <foc_motor_ld_lq_diff>0.00070143</foc_motor_ld_lq_diff>
    <foc_motor_r>1.7586</foc_motor_r>
    <foc_motor_flux_linkage>0.005777</foc_motor_flux_linkage>
    <foc_observer_gain>2.996e+07</foc_observer_gain>
    <foc_observer_gain_slow>0.05</foc_observer_gain_slow>
    <foc_observer_offset>-1</foc_observer_offset>
    <foc_duty_dowmramp_kp>10</foc_duty_dowmramp_kp>
    <foc_duty_dowmramp_ki>200</foc_duty_dowmramp_ki>
    <foc_openloop_rpm>1400</foc_openloop_rpm>
    <foc_openloop_rpm_low>0</foc_openloop_rpm_low>
    <foc_d_gain_scale_start>0.9</foc_d_gain_scale_start>
    <foc_d_gain_scale_max_mod>0.2</foc_d_gain_scale_max_mod>
    <foc_sl_openloop_hyst>0.1</foc_sl_openloop_hyst>
    <foc_sl_openloop_time_lock>0</foc_sl_openloop_time_lock>
    <foc_sl_openloop_time_ramp>0.1</foc_sl_openloop_time_ramp>
    <foc_sl_openloop_time>0.05</foc_sl_openloop_time>
    <foc_hall_table__0>255</foc_hall_table__0>
    <foc_hall_table__1>194</foc_hall_table__1>
    <foc_hall_table__2>128</foc_hall_table__2>
    <foc_hall_table__3>163</foc_hall_table__3>
    <foc_hall_table__4>63</foc_hall_table__4>
    <foc_hall_table__5>27</foc_hall_table__5>
    <foc_hall_table__6>95</foc_hall_table__6>
    <foc_hall_table__7>255</foc_hall_table__7>
    <foc_hall_interp_erpm>500</foc_hall_interp_erpm>
    <foc_sl_erpm>4000</foc_sl_erpm>
    <foc_sample_v0_v7>0</foc_sample_v0_v7>
    <foc_sample_high_current>0</foc_sample_high_current>
    <foc_sat_comp>0</foc_sat_comp>
    <foc_temp_comp>0</foc_temp_comp>
    <foc_temp_comp_base_temp>25</foc_temp_comp_base_temp>
    <foc_current_filter_const>0.1</foc_current_filter_const>
    <foc_cc_decoupling>0</foc_cc_decoupling>
    <foc_observer_type>0</foc_observer_type>
    <foc_hfi_voltage_start>20</foc_hfi_voltage_start>
    <foc_hfi_voltage_run>4</foc_hfi_voltage_run>
    <foc_hfi_voltage_max>10</foc_hfi_voltage_max>
    <foc_sl_erpm_hfi>2000</foc_sl_erpm_hfi>
    <foc_hfi_start_samples>15</foc_hfi_start_samples>
    <foc_hfi_obs_ovr_sec>0.001</foc_hfi_obs_ovr_sec>
    <foc_hfi_samples>1</foc_hfi_samples>
    <foc_offsets_cal_on_boot>1</foc_offsets_cal_on_boot>
    <foc_offsets_current__0>2116.8</foc_offsets_current__0>
    <foc_offsets_current__1>2077.99</foc_offsets_current__1>
    <foc_offsets_current__2>2069.98</foc_offsets_current__2>
    <foc_offsets_voltage__0>0.0002</foc_offsets_voltage__0>
    <foc_offsets_voltage__1>0.0019</foc_offsets_voltage__1>
    <foc_offsets_voltage__2>-0.0021</foc_offsets_voltage__2>
    <foc_offsets_voltage_undriven__0>0</foc_offsets_voltage_undriven__0>
    <foc_offsets_voltage_undriven__1>0</foc_offsets_voltage_undriven__1>
    <foc_offsets_voltage_undriven__2>0</foc_offsets_voltage_undriven__2>
    <foc_phase_filter_enable>1</foc_phase_filter_enable>
    <foc_phase_filter_max_erpm>4000</foc_phase_filter_max_erpm>
    <foc_mtpa_mode>0</foc_mtpa_mode>
    <foc_fw_current_max>0</foc_fw_current_max>
    <foc_fw_duty_start>0.9</foc_fw_duty_start>
    <foc_fw_q_current_factor>0.02</foc_fw_q_current_factor>
    <foc_fw_ramp_time>0.2</foc_fw_ramp_time>
    <gpd_buffer_notify_left>200</gpd_buffer_notify_left>
    <gpd_buffer_interpol>0</gpd_buffer_interpol>
    <gpd_current_filter_const>0.1</gpd_current_filter_const>
    <gpd_current_kp>0.03</gpd_current_kp>
    <gpd_current_ki>50</gpd_current_ki>
    <sp_pid_loop_rate>5</sp_pid_loop_rate>
    <s_pid_kp>0.004</s_pid_kp>
    <s_pid_ki>0.004</s_pid_ki>
    <s_pid_kd>0.0001</s_pid_kd>
    <s_pid_kd_filter>0.2</s_pid_kd_filter>
    <s_pid_min_erpm>900</s_pid_min_erpm>
    <s_pid_allow_braking>1</s_pid_allow_braking>
    <s_pid_ramp_erpms_s>25000</s_pid_ramp_erpms_s>
    <p_pid_kp>0.025</p_pid_kp>
    <p_pid_ki>0</p_pid_ki>
    <p_pid_kd>0</p_pid_kd>
    <p_pid_offset>0</p_pid_offset>
    <p_pid_kd_proc>0.00035</p_pid_kd_proc>
    <p_pid_kd_filter>0.2</p_pid_kd_filter>
    <p_pid_ang_div>1</p_pid_ang_div>
    <p_pid_gain_dec_angle>0</p_pid_gain_dec_angle>
    <cc_startup_boost_duty>0.01</cc_startup_boost_duty>
    <cc_min_current>0.05</cc_min_current>
    <cc_gain>0.0046</cc_gain>
    <cc_ramp_step_max>0.04</cc_ramp_step_max>
    <m_fault_stop_time_ms>500</m_fault_stop_time_ms>
    <m_duty_ramp_step>0.02</m_duty_ramp_step>
    <m_current_backoff_gain>0.5</m_current_backoff_gain>
    <m_encoder_counts>8192</m_encoder_counts>
    <m_sensor_port_mode>0</m_sensor_port_mode>
    <m_invert_direction>1</m_invert_direction>
    <m_drv8301_oc_mode>0</m_drv8301_oc_mode>
    <m_drv8301_oc_adj>16</m_drv8301_oc_adj>
    <m_bldc_f_sw_min>3000</m_bldc_f_sw_min>
    <m_bldc_f_sw_max>35000</m_bldc_f_sw_max>
    <m_dc_f_sw>25000</m_dc_f_sw>
    <m_ntc_motor_beta>3380</m_ntc_motor_beta>
    <m_out_aux_mode>0</m_out_aux_mode>
    <m_motor_temp_sens_type>0</m_motor_temp_sens_type>
    <m_ptc_motor_coeff>0.61</m_ptc_motor_coeff>
    <m_hall_extra_samples>1</m_hall_extra_samples>
    <si_motor_poles>14</si_motor_poles>
    <si_gear_ratio>1</si_gear_ratio>
    <si_wheel_diameter>0.083</si_wheel_diameter>
    <si_battery_type>0</si_battery_type>
    <si_battery_cells>7</si_battery_cells>
    <si_battery_ah>6</si_battery_ah>
    <si_motor_nl_current>1</si_motor_nl_current>
    <motor_brand>Unnamed</motor_brand>
    <motor_model>Not Specified</motor_model>
    <motor_weight>0</motor_weight>
    <motor_sensor_type>0</motor_sensor_type>
    <motor_description>&lt;!DOCTYPE HTML PUBLIC &quot;-//W3C//DTD HTML 4.0//EN&quot; &quot;http://www.w3.org/TR/REC-html40/strict.dtd&quot;&gt;
&lt;html&gt;&lt;head&gt;&lt;meta name=&quot;qrichtext&quot; content=&quot;1&quot; /&gt;&lt;style type=&quot;text/css&quot;&gt;
p, li { white-space: pre-wrap; }
&lt;/style&gt;&lt;/head&gt;&lt;body style=&quot; font-family:'Roboto'; font-size:12pt; font-weight:400; font-style:normal;&quot;&gt;
&lt;p style=&quot; margin-top:0px; margin-bottom:0px; margin-left:0px; margin-right:0px; -qt-block-indent:0; text-indent:0px;&quot;&gt;A motor description can be edited here.&lt;/p&gt;&lt;/body&gt;&lt;/html&gt;</motor_description>
    <motor_quality_bearings>0</motor_quality_bearings>
    <motor_quality_magnets>0</motor_quality_magnets>
    <motor_quality_construction>0</motor_quality_construction>
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

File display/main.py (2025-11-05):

import time
import json

from gpiozero import Button
from mqtt import Mqtt
from openmower import Openmower
from display import Display
from menu import Menu


class App:
    def __init__(self):
        # Buttons (GPIO pins)
        # Adjust pin numbers for your wiring layout
        self.buttonUp = Button(19, pull_up=True)
        self.buttonDown = Button(16, pull_up=True)
        self.buttonEnter = Button(26, pull_up=True)
        self.buttonDock = Button(20, pull_up=False)
        self.buttonPlay = Button(21, pull_up=False)

        self.menu = Menu()
        self.display = Display()
        self.mqtt = Mqtt()
        self.mqtt.mqtt_client.on_connect = self.mqtt_on_connect
        self.mqtt.mqtt_client.on_disconnect = self.mqtt_on_disconnect
        self.mqtt.mqtt_client.on_message = self.mqtt_on_message
        self.init_display()
        self.mqtt.connect()

    def init_display(self):
        self.display.clear()
        self.display.draw_background()
        self.display.draw_splash("Openmower")
        self.display.draw_message("MQTT connecting")

    def mqtt_on_connect(self, client, userdata, flags, rc):
        if rc == 0:
            print("Connected to MQTT Broker!")
            self.mqtt.subscribe(Openmower.topics.get_all())
            self.display.draw_message("MQTT connected")
        else:
            print(f"Failed to connect, return code {rc}")
            self.init_display()
        
    def mqtt_on_disconnect(self, client, userdata, rc):
        if rc != 0:
            print("Unexpected disconnection. Trying to reconnect...")
            self.init_display()
        else:
            print("Disconnected cleanly.")

    def mqtt_on_message(self, client, userdata, msg):
        topic = msg.topic
        message = msg.payload.decode()

        if topic == Openmower.topics.actions.name:
            Openmower.set_actions(json.loads(message))
            self.menu.set_actions()

        elif topic == Openmower.topics.robot_state.name:
            state = json.loads(message)
            if self.menu.is_active():
                return

            self.display.draw_mower_state(state["current_state"])
            self.display.draw_emergency(state["emergency"])
            self.display.draw_gps(
                state["pose"]["pos_accuracy"],
                state["gps_percentage"]
            )
            self.display.draw_battery(
                state["battery_percentage"],
                state["is_charging"]
            )

        elif topic == Openmower.topics.v_battery.name:
            if not self.menu.is_active():
                self.display.draw_battery_voltage(message)

    def mqtt_publish_message(self, topic, message):
        self.mqtt.publish_message(topic, message)

    def sleep(self):
        if not self.display.isAsleep:
            self.display.sleep()

    def wake(self):
        if self.display.isAsleep:
            self.display.wake()

def main():
    app = App()
    last_use = time.time()
    all_buttons_released = True

    while True:
        now = time.time()
        # Sleep after 60 seconds of inactivity
        # if now - last_use >= 60:
        #     app.sleep()

        button_pressed = False
        action = None

        if app.buttonPlay.is_pressed:
            print("play")
            button_pressed = True
            if all_buttons_released:
                if Openmower.actions.start_mowing.enabled:
                    action = Openmower.actions.start_mowing
                elif Openmower.actions.pause_mowing.enabled:
                    action = Openmower.actions.pause_mowing
                elif Openmower.actions.continue_mowing.enabled:
                    action = Openmower.actions.continue_mowing

        elif app.buttonDock.is_pressed:
            print("dock")
            button_pressed = True
            if all_buttons_released:
                action = Openmower.actions.abort_mowing

        elif app.buttonDown.is_pressed:
            print("down")
            button_pressed = True
            if all_buttons_released and not app.display.isAsleep:
                app.menu.go_down()
                app.display.draw_menu(
                    app.menu.current_item.title,
                    app.menu.current_item.subtitle,
                )

        elif app.buttonEnter.is_pressed:
            print("enter")
            button_pressed = True
            if all_buttons_released and not app.display.isAsleep:
                action = app.menu.current_item.action
                app.menu.enter()
                app.display.draw_menu(
                    app.menu.current_item.title,
                    app.menu.current_item.subtitle,
                )

        elif app.buttonUp.is_pressed:
            print("up")
            button_pressed = True
            if all_buttons_released and not app.display.isAsleep:
                app.menu.go_up()
                app.display.draw_menu(
                    app.menu.current_item.title,
                    app.menu.current_item.subtitle,
                )

        if all_buttons_released and button_pressed:
            last_use = time.time()
            if app.display.isAsleep:
                app.wake()
            elif action is not None and action.enabled:
                app.mqtt_publish_message("action", action.id)

        all_buttons_released = not button_pressed
        time.sleep(0.1)

if __name__ == "__main__":
    main()

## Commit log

2025-01-26 NEW: 3d models added
    [Ambrogio L30 Battery Mainboard holder.stl, Ambrogio L30 Pico display.stl, Ambrogio L30 Power switch board holder.stl]
2025-01-26 NEW: Pico firmware added
2025-01-29 CHG: Battery icons updated
2025-05-08 UPD: Readme.md updated
    [Ambrogio_L30_Drive_Motor.xml, Ambrogio_L30_Mower_Motor_10A.xml]
2025-05-24 NEW: Wiring diagram added
2025-10-28 NEW: Pico Zero W filles added
    [Ambrogio L30 Zero display.stl]
2025-11-05 Revise display installation instructions for clarity
    Updated instructions for Raspberry Pi display installation. Removed redundant steps and clarified connections.
2025-11-05 NEW: Rpi display without Rpi Zero
    [Ambrogio L30 display holder.stl]
2025-11-06 NEW: display wiring diagram added
2025-11-06 DEL: Old display files removed
    [Ambrogio L30 Pico display.stl, Ambrogio L30 Zero display.stl]
